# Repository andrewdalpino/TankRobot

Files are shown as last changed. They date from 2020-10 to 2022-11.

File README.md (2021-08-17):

# Autonomous Tank Robot
A curious little tank robot that loves to explore. Powered by a NodeMCU and guided by LiDAR and inertial sensing units, this robot can operate fully autonomously or in manual mode. It uses a combination of machine learning and control algorithms to navigate its environment.

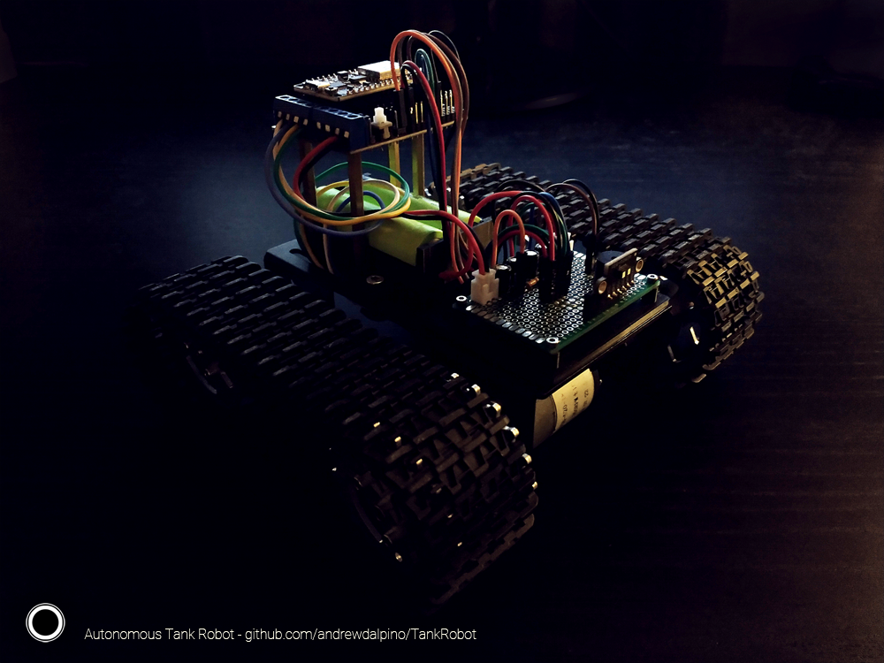
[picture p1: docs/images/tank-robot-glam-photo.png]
Tank Robot Glam Photo


## User Interface
Connect to Tank Robot's wireless access point and navigate the user interface using your favorite web browser. Tank Robot has a built-in HTTP server that accepts commands and emits events back to the UI in real-time.

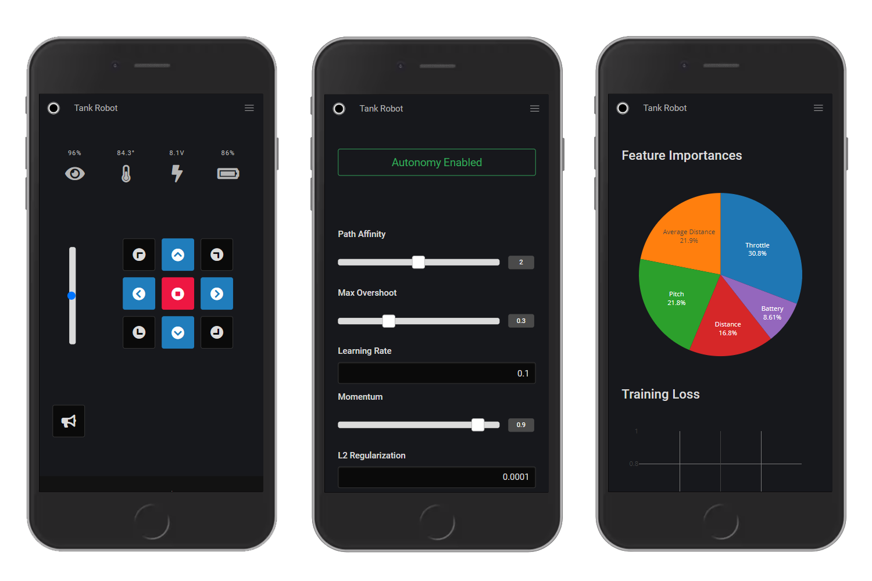
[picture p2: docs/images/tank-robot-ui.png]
Tank Robot User Interface


## Parts Used In This Project

- TP101 Robot Tank Platform
- NodeMCU 1.0 ESP-12E
- NodeMCU Motor Shield
- MPU-6050 Inertial Measurement Unit
- VL53L1X Laser ToF Range Sensor
- 3V Active Beeper
- 2 X 3.7V Lithium Ion 18650 Cells
- 2 X 33GB-520 12V 3500RPM Motors
- 6cm X 4cm Prototyping Board
- 4 X 16V 220μF Capacitors
- 1 X 220K Ohm Resistor
- 1 X 300K Ohm Resistor
- 3D Printed Board Mount
- 3D Printed MPU-6050 Mount
- 3D Printed 18650 Battery Holder
- 2 X 3D Printed Axle Bushings
- 2 X 2 Pin Male + Female JST Connectors
- 4 X M2x8 Socket Head Screws
- 1 X M3x8 Socket Head Screw
- 3 X M4x8 Socket Head Screws
- 3mm Double-sided Foam Tape

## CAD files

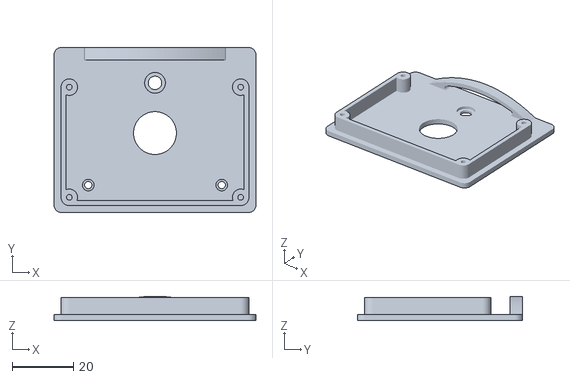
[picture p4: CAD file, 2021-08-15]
3d/board_mount.stl
66.0 x 54.0 x 8.00

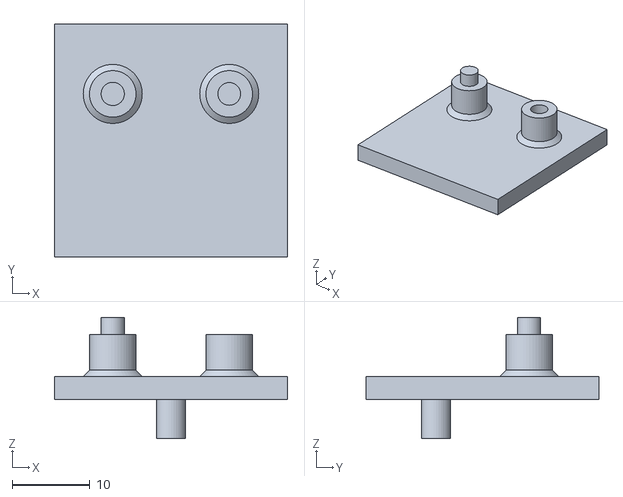
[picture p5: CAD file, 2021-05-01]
3d/mpu6050_mount.stl
30.0 x 30.0 x 15.6

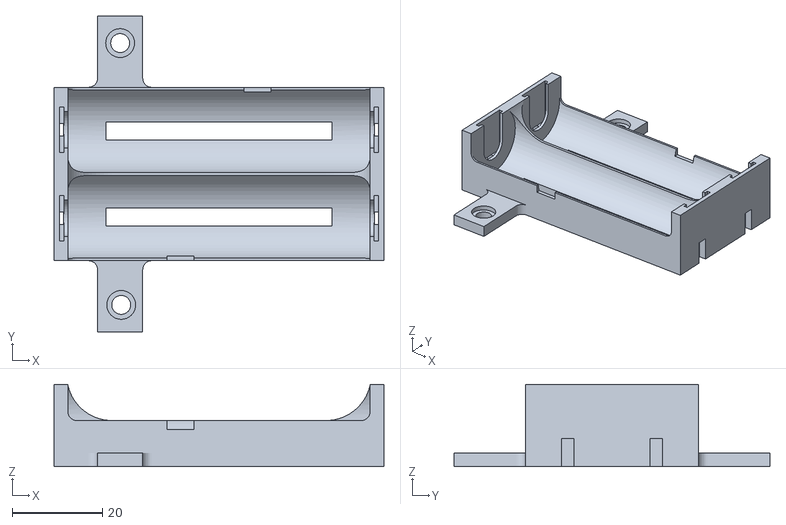
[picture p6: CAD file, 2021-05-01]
3d/battery_holder.stl
73.0 x 70.0 x 18.2

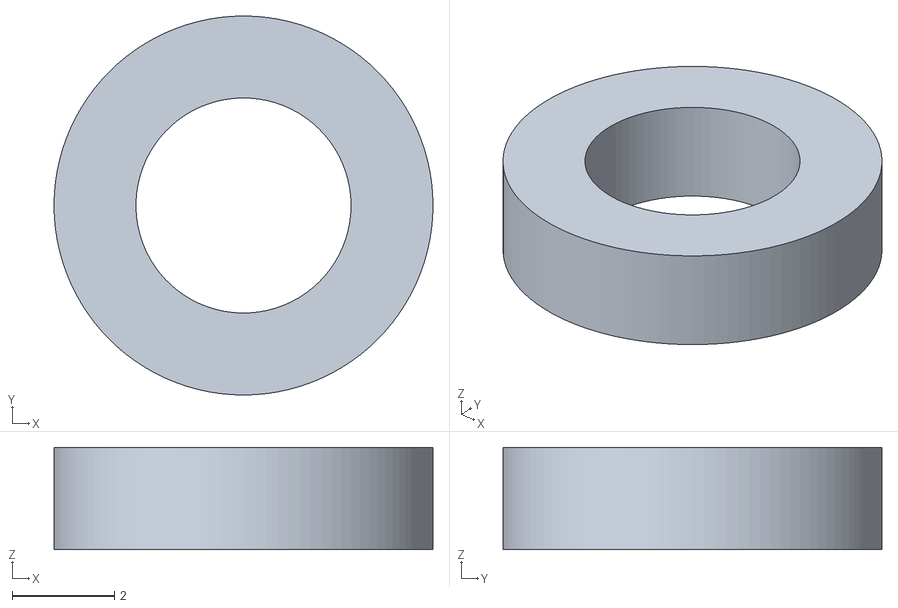
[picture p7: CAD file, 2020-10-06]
3d/axle_bushing.stl
7.40 x 7.40 x 2.00

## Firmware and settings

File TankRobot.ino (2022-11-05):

#include <ESP8266WiFi.h>
#include <ESPAsyncTCP.h>
#include <ESPAsyncWebServer.h>
#include <ArduinoJson.h>
#include <AsyncJson.h>
#include <VL53L1X.h>
#include <MPU6050_6Axis_MotionApps_V6_12.h>
#include <Ticker.h>
#include <Wire.h>
#include <FS.h>

#define SERIAL_BAUD 9600

#define BEEPER_PIN D7
#define BEEP_DURATION 100
#define BEEP_DELAY 30

#define AP_SSID "TankRobot"
#define AP_PASSWORD "KeepSummerSafe"
#define AP_CHANNEL 1
#define AP_MAX_CONNECTIONS 2
#define AP_HIDDEN 0

#define HTTP_PORT 80

#define HTTP_OK 200
#define HTTP_NOT_FOUND 404
#define HTTP_UNPROCESSABLE_ENTITY 422

#define BATTERY_PIN A0
#define BATTERY_SAMPLE_RATE 1000
#define VOLTMETER_RESOLUTION 1024.0
#define MIN_VOLTAGE 6.0
#define MAX_VOLTAGE 8.4

#define MOTOR_A_DIRECTION_PIN 0
#define MOTOR_A_THROTTLE_PIN 5
#define MOTOR_B_DIRECTION_PIN 2
#define MOTOR_B_THROTTLE_PIN 4
#define MIN_THROTTLE 800
#define MAX_THROTTLE 1000

#define FORWARD 1
#define REVERSE 0
#define LEFT 2
#define RIGHT 3

#define I2C_SDA_PIN D5
#define I2C_SCL_PIN D6
#define I2C_CLOCK 400000

#define MPU_ADDRESS 0x68
#define MPU_INTERRUPT_PIN 10
#define MPU_MAX_FIFO_COUNT 1024
#define LOW_PASS_FILTER_MODE 3
#define GYRO_CALIBRATION_LOOPS 8
#define QUATERNION_SAMPLE_RATE 20
#define GRAVITY_SAMPLE_RATE QUATERNION_SAMPLE_RATE
#define ORIENTATION_SAMPLE_RATE GRAVITY_SAMPLE_RATE
#define ACCEL_CALIBRATION_LOOPS 8
#define ACCEL_LSB_PER_G 16384.0
#define ACCELERATION_SAMPLE_RATE 50
#define IS_MOVING_SAMPLE_RATE ACCELERATION_SAMPLE_RATE
#define ZERO_MOVEMENT_THRESHOLD 0.13
#define ZERO_MOVEMENT_WINDOW 2
#define TEMPERATURE_SAMPLE_RATE 3000
#define TEMPERATURE_SENSITIVITY 340.0
#define TEMPERATURE_CONSTANT 36.53

#define ROTATOR_SAMPLE_RATE ORIENTATION_SAMPLE_RATE
#define ROTATOR_THRESHOLD 1.5 * DEG_TO_RAD

#define STABILIZER_SAMPLE_RATE ORIENTATION_SAMPLE_RATE

#define LIDAR_ADDRESS 0x52
#define LIDAR_TIMEOUT 500
#define LIDAR_SENSOR_OFFSET -10
#define LIDAR_TIMING_BUDGET 100000
#define LIDAR_SAMPLE_RATE 100
#define LIDAR_MAX_RANGE 3600
#define LIDAR_RANGE_VALID 0
#define LIDAR_NOISY_SIGNAL 1
#define LIDAR_SIGNAL_FAILURE 2
#define LIDAR_PHASE_OUT_OF_BOUNDS 4
#define VISIBILITY_SAMPLE_RATE 1000

#define EXPLORE_SAMPLE_RATE 250

#define SCAN_SAMPLE_RATE LIDAR_SAMPLE_RATE
#define SCAN_WINDOW 0.75 * PI
#define NUM_SCANS 5

#define MOVER_SAMPLE_RATE LIDAR_SAMPLE_RATE
#define MOVER_MAX_ACTIVATION 5000.0

#define COLLISION_SAMPLE_RATE LIDAR_SAMPLE_RATE
#define COLLISION_THRESHOLD 350

#define ROLLOVER_SAMPLE_RATE 500
#define ROLLOVER_THRESHOLD HALF_PI

#define MAX_RAND_INT 2147483647

Ticker beep_timer;

const IPAddress _ip(192, 168, 4, 1);
const IPAddress _gateway(192, 168, 4, 1);
const IPAddress _subnet(255, 255, 255, 0);

AsyncWebServer server(HTTP_PORT);

AsyncEventSource sensor_emitter("/events/robot/sensors");
AsyncEventSource training_emitter("/events/robot/training");
AsyncEventSource malfunction_emitter("/events/robot/malfunctions");

float _battery_voltage;

Ticker battery_timer;

uint8_t _direction = FORWARD;
unsigned int _throttle = 900;
bool _stopped = true;

Ticker brake_timer;

MPU6050 mpu(MPU_ADDRESS);

Quaternion _q;
VectorFloat _gravity;
VectorFloat _acceleration;
float _heading, _pitch, _roll;
float _heading_lock;
float _temperature;
bool _is_moving;
uint8_t _zero_movement_count;
uint8_t _dmp_fifo_buffer[64];
uint16_t _dmp_packet_size;
volatile bool _dmp_ready = false;
void IRAM_ATTR dmpDataReady();

Ticker quaternion_timer, gravity_timer, orientation_timer;
Ticker acceleration_timer, is_moving_timer;
Ticker temperature_timer;

float _rotator_p_gain = 2.0;
float _rotator_i_gain = 0.7;
float _rotator_d_gain = 1.4;

float _stabilizer_p_gain = 0.4;
float _stabilizer_i_gain = 0.8;
float _stabilizer_d_gain = 0.3;

float _rotator_prev_delta, _rotator_delta_integral;
float _stabilizer_prev_delta, _stabilizer_delta_integral;

Ticker rotator_timer, stabilizer_timer;
Ticker rollover_timer;

VL53L1X lidar;

float _scan_angles[NUM_SCANS];
float _angle_visibilities[NUM_SCANS];
unsigned int _distances_to_object[NUM_SCANS];
uint8_t _scan_direction = LEFT;
uint8_t _scan_count;

Ticker scan_timer, collision_timer, visibility_timer;

float _path_affinity = 2.0;

float _mover_learning_rate = 0.1;
float _mover_momentum = 0.9;
float _mover_alpha = 1e-4;
float _mover_max_overshoot = 0.2;
float _mover_features[4];
float _mover_weights[4];
float _mover_weight_velocities[4];
float _mover_bias;
float _mover_bias_velocity;
float _mover_prediction;
unsigned long _mover_start_timestamp;
unsigned long _mover_end_timestamp;
unsigned int _mover_epoch = 1;

Ticker mover_timer;

uint8_t _explorer_step;

Ticker explore_timer;

void forward(unsigned int duration = 0);
void reverse(unsigned int duration = 0);

/**
 * Set up the serial interface.
 */
void setupSerial()
{
    Serial.begin(SERIAL_BAUD);

    Serial.println("Serial port enabled");
}

/**
 * Setup the beeper.
 */
void setupBeeper()
{
    pinMode(BEEPER_PIN, OUTPUT);

    Serial.println("Beeper enabled");
}

/**
 * Set up the central processing unit.
 */
void setupCPU()
{
    Serial.print("CPU speed: ");
    Serial.print(ESP.getCpuFreqMHz());
    Serial.println("mhz");
}

/**
 * Setup the flash ROM.
 */
void setupROM()
{
    if (!ESP.checkFlashCRC()) {
        Serial.println("Flash ROM CRC mismatch");

        panicNow();
    }

    Serial.print("ROM speed: ");
    Serial.print(ESP.getFlashChipSpeed() / 1000000);
    Serial.println("mhz");

    Serial.print("ROM size: ");
    Serial.print(ESP.getFlashChipRealSize() / 1024);
    Serial.println("kb");

    Serial.print("Free space: ");
    Serial.print(ESP.getFreeSketchSpace() / 1024.0, 1);
    Serial.println("kb");
}

/**
 * Set up the SPI Flash Filesystem.
 */
void setupSPIFFS()
{
    if (SPIFFS.begin()) {
        Serial.println("SPIFFS mounted");
    } else {
        Serial.println("Failed to mount SPIFFS");

        panicNow();
    }
}

/**
 * Set up the wireless access point.
 */
void setupAccessPoint()
{
    WiFi.softAPConfig(_ip, _gateway, _subnet);
    WiFi.softAP(AP_SSID, AP_PASSWORD, AP_CHANNEL, AP_HIDDEN, AP_MAX_CONNECTIONS);

    Serial.println("Access point ready");
    Serial.print("SSID: ");
    Serial.println(AP_SSID);
    Serial.print("IP Address: ");
    Serial.println(WiFi.softAPIP());
    Serial.print("MAC Address: ");
    Serial.println(WiFi.softAPmacAddress());
}

/**
 * Set up the HTTP server.
 */
void setupHttpServer()
{
    setupStaticRoutes();

    setupApiRoutes();

    setupEventEmitters();

    server.onNotFound(handleNotFound);

    server.begin();

    Serial.print("HTTP server listening on port ");
    Serial.println(HTTP_PORT);
}

/**
 * Set up the HTTP static routes.
 */
void setupStaticRoutes()
{
    server.serveStatic("/ui", SPIFFS, "/app.html");
    server.serveStatic("/ui/control", SPIFFS, "/app.html");
    server.serveStatic("/ui/dynamics", SPIFFS, "/app.html");
    server.serveStatic("/ui/autonomy", SPIFFS, "/app.html");
    server.serveStatic("/ui/training", SPIFFS, "/app.html");
    server.serveStatic("/manifest.json", SPIFFS, "/manifest.json");
    server.serveStatic("/app.js", SPIFFS, "/app.js");
    server.serveStatic("/sw.js", SPIFFS, "/sw.js");
    server.serveStatic("/app.css", SPIFFS, "/app.css");
    server.serveStatic("/images/app-icon-small.png", SPIFFS, "/images/app-icon-small.png");
    server.serveStatic("/images/app-icon-large.png", SPIFFS, "/images/app-icon-large.png");
    server.serveStatic("/fonts/Roboto-300.woff2", SPIFFS, "/fonts/Roboto-300.woff2");
    server.serveStatic("/fonts/Roboto-regular.woff2", SPIFFS, "/fonts/Roboto-regular.woff2");
    server.serveStatic("/fonts/Roboto-500.woff2", SPIFFS, "/fonts/Roboto-500.woff2");
    server.serveStatic("/fonts/fa-solid-900.woff2", SPIFFS, "/fonts/fa-solid-900.woff2");
    server.serveStatic("/sounds/plucky.ogg", SPIFFS, "/sounds/plucky.ogg");
}

/**
 * Set up the HTTP API routes.
 */
void setupApiRoutes()
{
    server.addHandler(new AsyncCallbackJsonWebHandler("/robot/motors/direction", handleChangeDirection));
    server.addHandler(new AsyncCallbackJsonWebHandler("/robot/motors/throttle", handleSetThrottlePercentage));
    server.addHandler(new AsyncCallbackJsonWebHandler("/robot/rotator/left", handleRotateLeft));
    server.addHandler(new AsyncCallbackJsonWebHandler("/robot/rotator/right", handleRotateRight));
    server.addHandler(new AsyncCallbackJsonWebHandler("/robot/rotator/p", handleSetRotatorPGain));
    server.addHandler(new AsyncCallbackJsonWebHandler("/robot/rotator/i", handleSetRotatorIGain));
    server.addHandler(new AsyncCallbackJsonWebHandler("/robot/rotator/d", handleSetRotatorDGain));
    server.addHandler(new AsyncCallbackJsonWebHandler("/robot/autonomy/path-affinity", handleSetPathAffinity));
    server.addHandler(new AsyncCallbackJsonWebHandler("/robot/autonomy/mover/max-overshoot", handleSetMoverMaxOvershoot));
    server.addHandler(new AsyncCallbackJsonWebHandler("/robot/autonomy/mover/learning-rate", handleSetMoverLearningRate));
    server.addHandler(new AsyncCallbackJsonWebHandler("/robot/autonomy/mover/momentum", handleSetMoverMomentum));
    server.addHandler(new AsyncCallbackJsonWebHandler("/robot/autonomy/mover/alpha", handleSetMoverAlpha));
    server.addHandler(new AsyncCallbackJsonWebHandler("/robot/stabilizer/p", handleSetStabilizerPGain));
    server.addHandler(new AsyncCallbackJsonWebHandler("/robot/stabilizer/i", handleSetStabilizerIGain));
    server.addHandler(new AsyncCallbackJsonWebHandler("/robot/stabilizer/d", handleSetStabilizerDGain));

    server.on("/robot", HTTP_GET, handleGetRobot);
    server.on("/robot/motors", HTTP_DELETE, handleStop);
    server.on("/robot/features/beeper", HTTP_PUT, handleBeep);
    server.on("/robot/autonomy/enabled", HTTP_PUT, handleExplore);
    server.on("/robot/autonomy", HTTP_DELETE, handleStop);
}

/**
 * Set up the HTTP event emitters.
 */
void setupEventEmitters()
{
    server.addHandler(&sensor_emitter);
    server.addHandler(&training_emitter);
    server.addHandler(&malfunction_emitter);
}

/**
 * Set up the battery voltmeter.
 */
void setupBattery()
{
    pinMode(BATTERY_PIN, INPUT);

    battery_timer.attach_ms(BATTERY_SAMPLE_RATE, updateBattery);

    Serial.println("Battery voltmeter enabled");
}

/**
 * Set up the motors.
 */
void setupMotors()
{
    pinMode(MOTOR_A_DIRECTION_PIN, OUTPUT);
    pinMode(MOTOR_A_THROTTLE_PIN, OUTPUT);

    pinMode(MOTOR_B_DIRECTION_PIN, OUTPUT);
    pinMode(MOTOR_B_THROTTLE_PIN, OUTPUT);

    analogWriteFreq(MAX_THROTTLE);

    Serial.println("Motors enabled");
}

/**
 * Set up the I2C bus.
 */
void setupI2C()
{
    Wire.begin(I2C_SDA_PIN, I2C_SCL_PIN);

    Wire.setClock(I2C_CLOCK);

    Serial.println("I2C bus initialized");
}

/**
 * Set up and calibrate the MPU accelerometer, gyroscope, and temperature sensor.
 */
void setupMPU()
{
    mpu.initialize();

    if (mpu.testConnection()) {
        Serial.println("MPU initialized");
    } else {
        Serial.println("MPU failure");

        panicNow();
    }

    pinMode(MPU_INTERRUPT_PIN, INPUT);

    attachInterrupt(digitalPinToInterrupt(MPU_INTERRUPT_PIN), dmpDataReady, RISING);

    mpu.setFullScaleGyroRange(MPU6050_GYRO_FS_250);
    mpu.setFullScaleAccelRange(MPU6050_ACCEL_FS_2);

    mpu.setDLPFMode(LOW_PASS_FILTER_MODE);

    Serial.print("Calibrating gyroscope ");
    mpu.CalibrateGyro(GYRO_CALIBRATION_LOOPS);
    Serial.println(" done");

    Serial.print("Calibrating accelerometer ");
    mpu.CalibrateAccel(ACCEL_CALIBRATION_LOOPS);
    Serial.println(" done");

    mpu.setSleepEnabled(false);

    mpu.dmpInitialize();

    mpu.setDMPEnabled(true);

    _dmp_packet_size = mpu.dmpGetFIFOPacketSize();

    quaternion_timer.attach_ms(QUATERNION_SAMPLE_RATE, updateQuaternion);
    gravity_timer.attach_ms(GRAVITY_SAMPLE_RATE, updateGravity);
    orientation_timer.attach_ms(ORIENTATION_SAMPLE_RATE, updateOrientation);
    acceleration_timer.attach_ms(ACCELERATION_SAMPLE_RATE, updateAcceleration);
    is_moving_timer.attach_ms(IS_MOVING_SAMPLE_RATE, updateIsMoving);
    temperature_timer.attach_ms(TEMPERATURE_SAMPLE_RATE, updateTemperature);

    Serial.println("DMP initialized");
}

/**
 * Set up the lidar distance sensor.
 */
void setupLidar()
{
    lidar.setTimeout(LIDAR_TIMEOUT);

    if (lidar.init()) {
        Serial.println("Lidar initialized");
    } else {
        Serial.println("Lidar failure");

        panicNow();
    }

    lidar.setDistanceMode(VL53L1X::Long);
    lidar.setMeasurementTimingBudget(LIDAR_TIMING_BUDGET);
    lidar.startContinuous(LIDAR_SAMPLE_RATE);

    visibility_timer.attach_ms(VISIBILITY_SAMPLE_RATE, updateVisibility);
}

/**
 * Set up the random number generator.
 */
void setupRandom()
{
    randomSeed(RANDOM_REG32);

    Serial.println("Seeded random number generator");
}

/**
 * Set up the mover model.
 */
void setupMover()
{
    for (uint8_t i = 0; i < 5; ++i) {
        _mover_weights[i] = random(-MAX_RAND_INT, MAX_RAND_INT) / (float)MAX_RAND_INT;
    }

    Serial.println("Mover model initialized");
}

/**
 * Bootstrap the robot.
 */
void setup()
{
    setupSerial();

    setupBeeper();

    setupCPU();
    setupROM();

    setupSPIFFS();

    setupAccessPoint();
    setupHttpServer();

    setupBattery();

    setupMotors();

    setupI2C();
    setupMPU();
    setupLidar();

    setupRandom();

    setupMover();

    Serial.println("Ready");
}

/**
 * The main event loop.
 */
void loop()
{
    if (lidar.dataReady()) {
        lidar.read(false);
    }

    yield();

    if (_dmp_ready) {
        uint8_t mpu_int_status = mpu.getIntStatus();

        uint16_t fifo_count = mpu.getFIFOCount();

        if (mpu_int_status & 0x10 || fifo_count >= MPU_MAX_FIFO_COUNT) {
            mpu.resetFIFO();
        } else if (fifo_count % _dmp_packet_size != 0) {
            mpu.resetFIFO();
        } else if (mpu_int_status & 0x02) {
            while (fifo_count >= _dmp_packet_size) {
                mpu.getFIFOBytes(_dmp_fifo_buffer, _dmp_packet_size);

                fifo_count -= _dmp_packet_size;
            }
        }

        _dmp_ready = false;
    }
}

/**
 * Handle a get robot info request.
 */
void handleGetRobot(AsyncWebServerRequest *request)
{
    StaticJsonDocument<768> doc;
    char buffer[768];

    JsonObject robot = doc.createNestedObject("robot");

    JsonObject motors = robot.createNestedObject("motors");

    motors["direction"] = _direction;
    motors["throttle"] = throttlePercentage();
    motors["stopped"] = _stopped;

    JsonObject sensors = robot.createNestedObject("sensors");

    JsonObject battery = sensors.createNestedObject("battery");

    battery["voltage"] = _battery_voltage;
    battery["capacity"] = batteryCapacity();

    JsonObject lidar = sensors.createNestedObject("lidar");

    lidar["visibility"] = visibility();

    sensors["temperature"] = _temperature;

    JsonObject rotator = robot.createNestedObject("rotator");

    rotator["p"] = _rotator_p_gain;
    rotator["i"] = _rotator_i_gain;
    rotator["d"] = _rotator_d_gain;

    JsonObject autonomy = robot.createNestedObject("autonomy");

    autonomy["enabled"] = isAutonomous();
    autonomy["pathAffinity"] = _path_affinity;

    JsonObject mover = autonomy.createNestedObject("mover");

    mover["learningRate"] = _mover_learning_rate;
    mover["momentum"] = _mover_momentum;
    mover["alpha"] = _mover_alpha;
    mover["maxOvershoot"] = _mover_max_overshoot;

    JsonObject importances = mover.createNestedObject("importances");

    importances["throttle"] = moverThrottleImportance();
    importances["battery"] = moverBatteryImportance();
    importances["pitch"] = moverPitchImportance();
    importances["distance"] = moverDistanceImportance();

    JsonObject stabilizer = robot.createNestedObject("stabilizer");

    stabilizer["p"] = _stabilizer_p_gain;
    stabilizer["i"] = _stabilizer_i_gain;
    stabilizer["d"] = _stabilizer_d_gain;

    serializeJson(doc, buffer);

    request->send(HTTP_OK, "application/json", buffer);
}

/**
 * Handle a change direction request.
 */
void handleChangeDirection(AsyncWebServerRequest *request, JsonVariant &json)
{
    const JsonObject &doc = json.as<JsonObject>();

    if (!doc.containsKey("direction")) {
        request->send(HTTP_UNPROCESSABLE_ENTITY);

        return;
    }

    uint8_t direction = doc["direction"];

    switch (direction) {
        case FORWARD:
            forward();

            break;

        case LEFT:
            left();

            break;

        case RIGHT:
            right();

            break;

        case REVERSE:
            reverse();

            break;
    }

    request->send(HTTP_OK);
}

/**
 * Handle the stop movement request.
 */
void handleStop(AsyncWebServerRequest *request)
{
    stop();

    request->send(HTTP_OK);
}

/**
 * Handle a beep request.
 */
void handleBeep(AsyncWebServerRequest *request)
{
    beep(2);

    request->send(HTTP_OK);
}

/**
 * Handle the explore request.
 */
void handleExplore(AsyncWebServerRequest *request)
{
    explore();

    request->send(HTTP_OK);
}

/**
 * Handle a set throttle position request.
 */
void handleSetThrottlePercentage(AsyncWebServerRequest *request, JsonVariant &json)
{
    const JsonObject &doc = json.as<JsonObject>();

    if (!doc.containsKey("throttle")) {
        request->send(HTTP_UNPROCESSABLE_ENTITY);

        return;
    }

    setThrottlePercentage(doc["throttle"]);

    request->send(HTTP_OK);
}

/**
 * Handle the rotate left request.
 */
void handleRotateLeft(AsyncWebServerRequest *request, JsonVariant &json)
{
    const JsonObject &doc = json.as<JsonObject>();

    if (!doc.containsKey("radians")) {
        request->send(HTTP_UNPROCESSABLE_ENTITY);

        return;
    }

    rotateLeft(doc["radians"]);

    request->send(HTTP_OK);
}

/**
 * Handle the rotate right request.
 */
void handleRotateRight(AsyncWebServerRequest *request, JsonVariant &json)
{
    const JsonObject &doc = json.as<JsonObject>();

    if (!doc.containsKey("radians")) {
        request->send(HTTP_UNPROCESSABLE_ENTITY);

        return;
    }

    rotateRight(doc["radians"]);

    request->send(HTTP_OK);
}

/**
 * Handle the set rotator proportional control gain.
 */
void handleSetRotatorPGain(AsyncWebServerRequest *request, JsonVariant &json)
{
    const JsonObject &doc = json.as<JsonObject>();

    if (!doc.containsKey("gain")) {
        request->send(HTTP_UNPROCESSABLE_ENTITY);

        return;
    }

    setRotatorPGain(doc["gain"]);

    request->send(HTTP_OK);
}

/**
 * Handle the set rotator integral control gain.
 */
void handleSetRotatorIGain(AsyncWebServerRequest *request, JsonVariant &json)
{
    const JsonObject &doc = json.as<JsonObject>();

    if (!doc.containsKey("gain")) {
        request->send(HTTP_UNPROCESSABLE_ENTITY);

        return;
    }

    setRotatorIGain(doc["gain"]);

    request->send(HTTP_OK);
}

/**
 * Handle the set rotator derivative control gain.
 */
void handleSetRotatorDGain(AsyncWebServerRequest *request, JsonVariant &json)
{
    const JsonObject &doc = json.as<JsonObject>();

    if (!doc.containsKey("gain")) {
        request->send(HTTP_UNPROCESSABLE_ENTITY);

        return;
    }

    setRotatorDGain(doc["gain"]);

    request->send(HTTP_OK);
}

/**
 * Handle the set path affinity request.
 */
void handleSetPathAffinity(AsyncWebServerRequest *request, JsonVariant &json)
{
    const JsonObject &doc = json.as<JsonObject>();

    if (!doc.containsKey("pathAffinity")) {
        request->send(HTTP_UNPROCESSABLE_ENTITY);

        return;
    }

    setPathAffinity(doc["pathAffinity"]);

    request->send(HTTP_OK);
}

/**
 * Handle the set mover max overshoot request.
 */
void handleSetMoverMaxOvershoot(AsyncWebServerRequest *request, JsonVariant &json)
{
    const JsonObject &doc = json.as<JsonObject>();

    if (!doc.containsKey("maxOvershoot")) {
        request->send(HTTP_UNPROCESSABLE_ENTITY);

        return;
    }

    setMoverMaxOvershoot(doc["maxOvershoot"]);

    request->send(HTTP_OK);
}

/**
 * Handle the set mover learning rate request.
 */
void handleSetMoverLearningRate(AsyncWebServerRequest *request, JsonVariant &json)
{
    const JsonObject &doc = json.as<JsonObject>();

    if (!doc.containsKey("learningRate")) {
        request->send(HTTP_UNPROCESSABLE_ENTITY);

        return;
    }

    setMoverLearningRate(doc["learningRate"]);

    request->send(HTTP_OK);
}

/**
 * Handle the set mover momentum request.
 */
void handleSetMoverMomentum(AsyncWebServerRequest *request, JsonVariant &json)
{
    const JsonObject &doc = json.as<JsonObject>();

    if (!doc.containsKey("momentum")) {
        request->send(HTTP_UNPROCESSABLE_ENTITY);

        return;
    }

    setMoverMomentum(doc["momentum"]);

    request->send(HTTP_OK);
}

/**
 * Handle the set mover L2 regularization parameter.
 */
void handleSetMoverAlpha(AsyncWebServerRequest *request, JsonVariant &json)
{
    const JsonObject &doc = json.as<JsonObject>();

    if (!doc.containsKey("alpha")) {
        request->send(HTTP_UNPROCESSABLE_ENTITY);

        return;
    }

    setMoverAlpha(doc["alpha"]);

    request->send(HTTP_OK);
}

/**
 * Handle the set stabilizer proportional control gain.
 */
void handleSetStabilizerPGain(AsyncWebServerRequest *request, JsonVariant &json)
{
    const JsonObject &doc = json.as<JsonObject>();

    if (!doc.containsKey("gain")) {
        request->send(HTTP_UNPROCESSABLE_ENTITY);

        return;
    }

    setStabilizerPGain(doc["gain"]);

    request->send(HTTP_OK);
}

/**
 * Handle the set stabilizer integral control gain.
 */
void handleSetStabilizerIGain(AsyncWebServerRequest *request, JsonVariant &json)
{
    const JsonObject &doc = json.as<JsonObject>();

    if (!doc.containsKey("gain")) {
        request->send(HTTP_UNPROCESSABLE_ENTITY);

        return;
    }

    setStabilizerIGain(doc["gain"]);

    request->send(HTTP_OK);
}
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

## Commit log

2019-09-24 Added battery and voltage indicator
2019-09-24 Added rudimentary stability assist
    [TankRobot.ino]
2019-09-27 Added MPU temperature monitoring
2019-10-03 Added sonar and rotations
2020-05-20 Added board and sensor mounts
    [board_mounts.stl, mpu_6050_mount.stl, mpu_6500_mount.stl]
2020-05-21 Added PID rotator control
2020-06-07 Added battery undervoltage protection
2020-10-06 Update 3d files
    [axle_bushing.stl, battery_holder.stl, board_mounts.stl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]
2021-05-01 Add rotations
    [axle_spacer.stl, battery_holder.stl, board_mount.stl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]
2021-05-01 Long beep on battery undervoltage
2021-05-02 Refactor IMU equations
2021-05-08 Add bias velocity and norm
2021-05-09 Revert "Move by displacement"
    This reverts commit 60fa082542eb1ecceec1965c4bb2993171ae8bf1.
    [TankRobot.ino]
2021-05-19 Add lidar acuity
2021-05-19 Consider lidar visibility when planning
2021-05-20 Some tweaks
    Add lidar acuity
2021-05-20 Remove MPU-6500 mount 3D model
    [mpu6500_mount.stl]
2021-05-20 Improved motion detection
    [axle_bushing.stl]
2021-05-22 Update board mount
    [board_mount.stl]
2021-08-15 Add wall to board mount
    [board_mount.stl]
2021-08-17 Back up on collision
    [TankRobot.ino]
